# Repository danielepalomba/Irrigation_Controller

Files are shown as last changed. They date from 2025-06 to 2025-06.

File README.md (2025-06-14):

# Irrigation-Controller

## Introduction

This project stems from the need to automate the irrigation of my house's garden so as to make the job easier for my now elderly grandfather. To do this, I decided to build an irrigation control unit that would integrate perfectly with **Home Assistant** already in operation in my house.

## PCB and electrical components

*Caution: 230V mains current can be fatal, in case of doubt or uncertainty, consult a professional!*

First of all, I studied the electrical system, specifically the garden is divided into 3 zones each containing sprinklers controlled by a 24V AC solenoid valve. So as a first step, I installed a transformer that would allow me to obtain the desired voltage from the mains current. Once the power system was complete, I started to study the actual electrical system of the control unit.

The basic idea was to build a control unit consisting mainly of **three modules**:

- *Main board*

- *Relay board*

- *Soil moisture sensor*

There is one problem, however. The ESP32, relay board and sensor are powered by DC, not 24V AC. I therefore installed an AC-DC converter with 12V 5A DC output. 

At this point you may be asking yourself, *Why 12V? It is not possible to power the esp32 with this voltage.* The answer is simple, the relay board needs to be powered at 12V, so to power the esp32 we will need an additional step-down module. Specifically, I chose one based on the LM2596.

So I set to work and using KiCad I created the circuit diagram. 

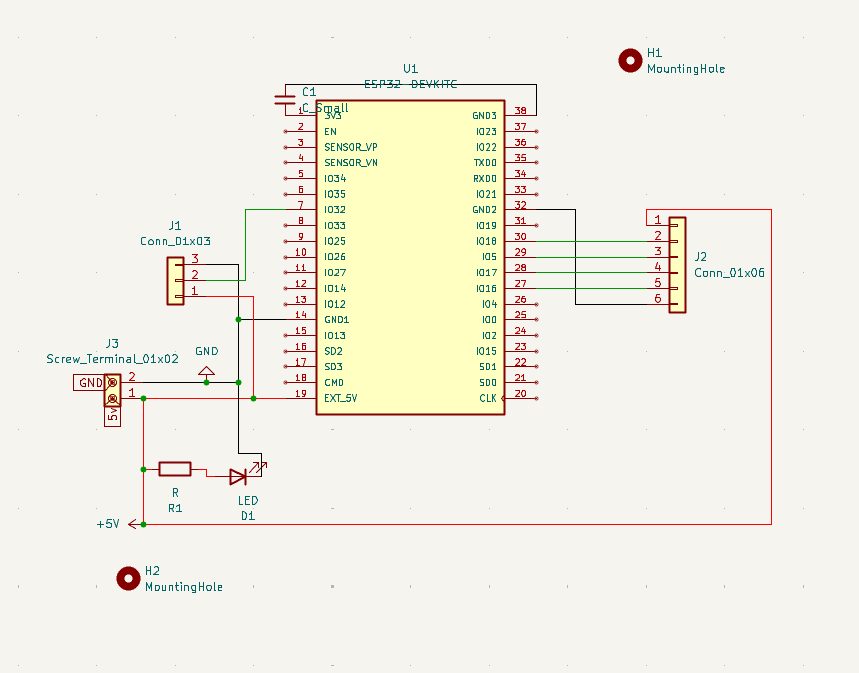
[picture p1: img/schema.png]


- J1, will handle the soil moisture sensor.

- J2 will manage the relay board.

- D1 is simply a status LED.

- C1 is a decoupling capacitor, useful for reducing interference when supplying the board with external 5V.  It should be connected as close as possible to the 3.3V pin.

I then moved on to the modelling of the actual PCB.

 The board will consist of two layers, the upper one for current delivery and the lower one for signal transport. The tracks carrying current to the modules are 0.5mm while those carrying signals are 0.25mm. I then defined the 3mm mounting holes and inserted a ground plane both above and below the board.

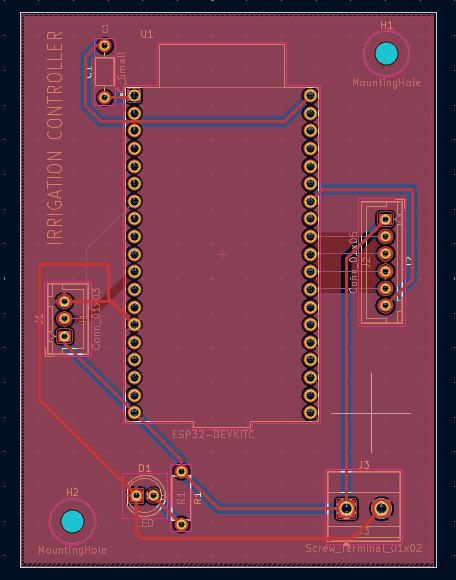
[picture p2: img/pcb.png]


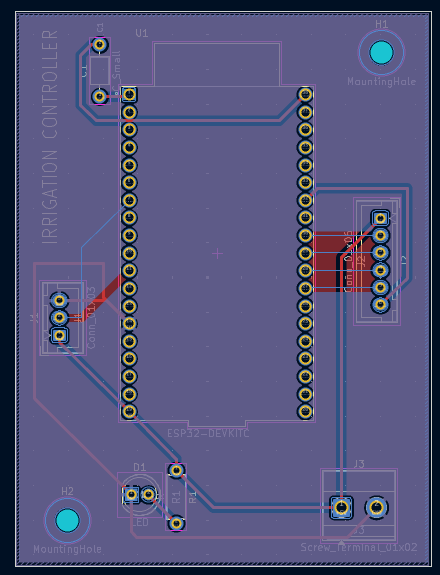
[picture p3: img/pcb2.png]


Once I had completed the card, I sent it to print........and here it is!

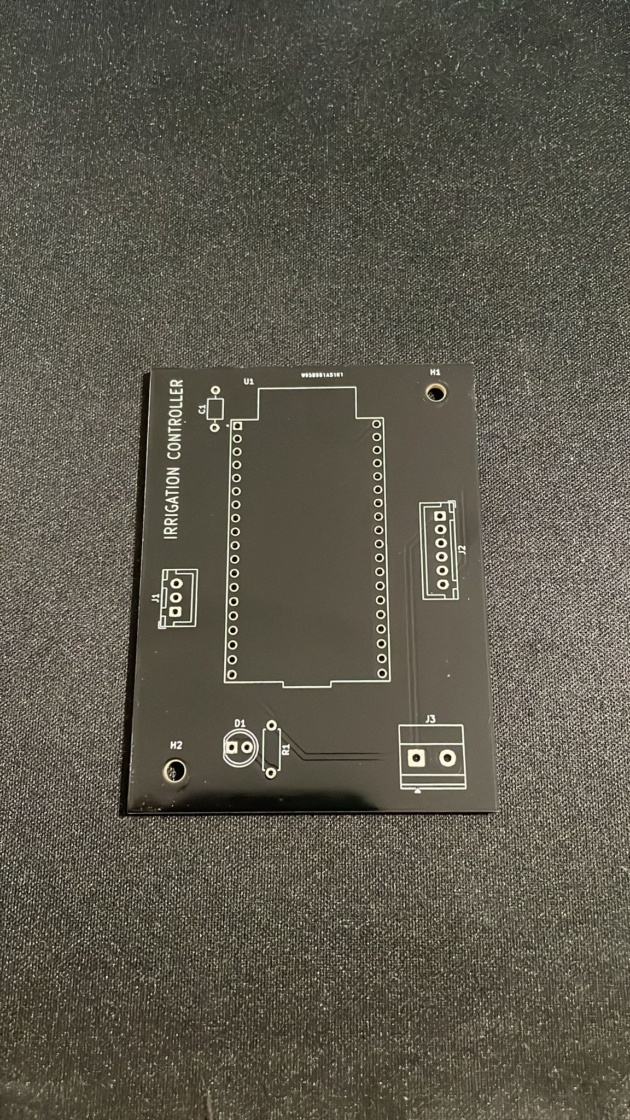
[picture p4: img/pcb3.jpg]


Now that the board was with me, I started soldering all the components. Specifically:

- J3: TerminalBlock_Phoenix:TerminalBlock_Phoenix_MKDS-1,5-2-5.08_1x02_P5.08mm_Horizontal

- R1: 1k Ohm Resistor_THT:R_Axial_DIN0207_L6.3mm_D2.5mm_P7.62mm_Horizontal

- D1 5mm LED

- J1: Connector_JST:JST_XH_B3B-XH-A_1x03_P2.50mm_Vertical

- J2: Connector_JST:JST_XH_B6B-XH-A_1x06_P2.50mm_Vertical

- C1: Capacitor_THT:C_Axial_L3.8mm_D2.6mm_P7.50mm_Horizontal

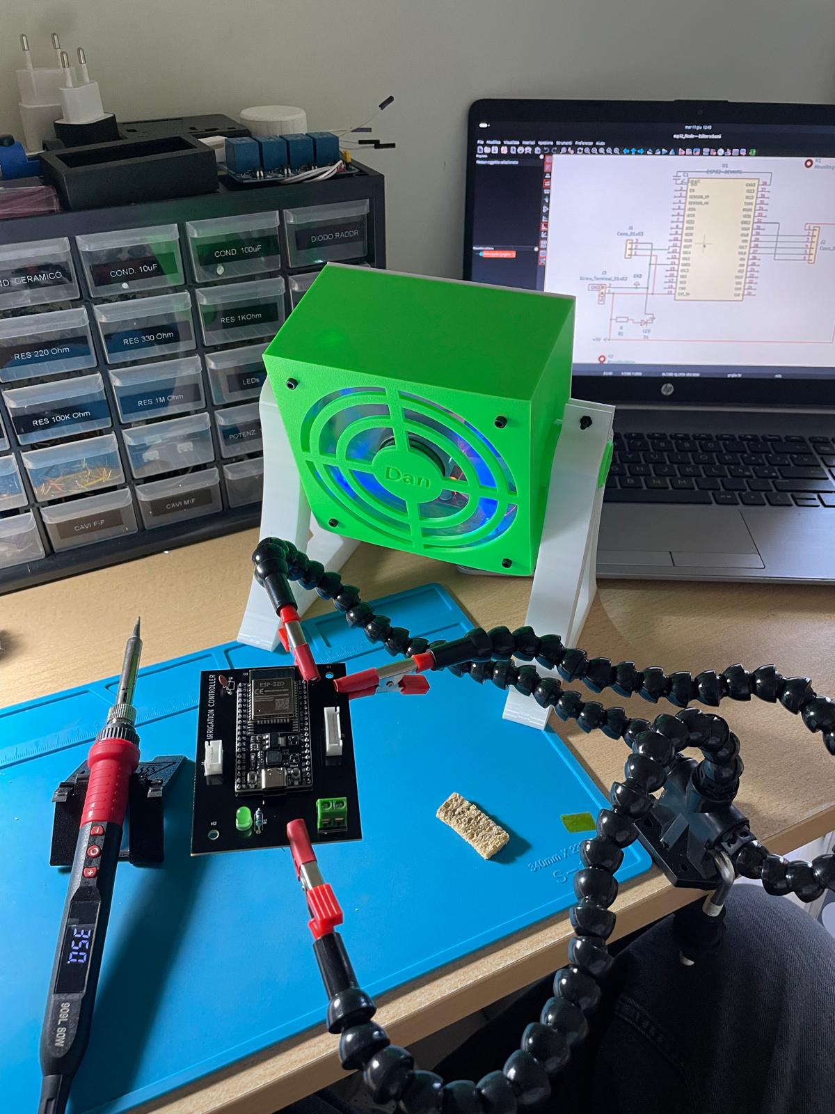
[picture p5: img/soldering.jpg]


The board is finally finished, after which I started thinking of a way to waterproof the soil moisture sensor so that it would withstand the elements.

In the end I modelled a box and printed it with my 3D printer using PETG.  I then inserted the critical part of the board inside and filled the box with epoxy resin.

And this is the end result.

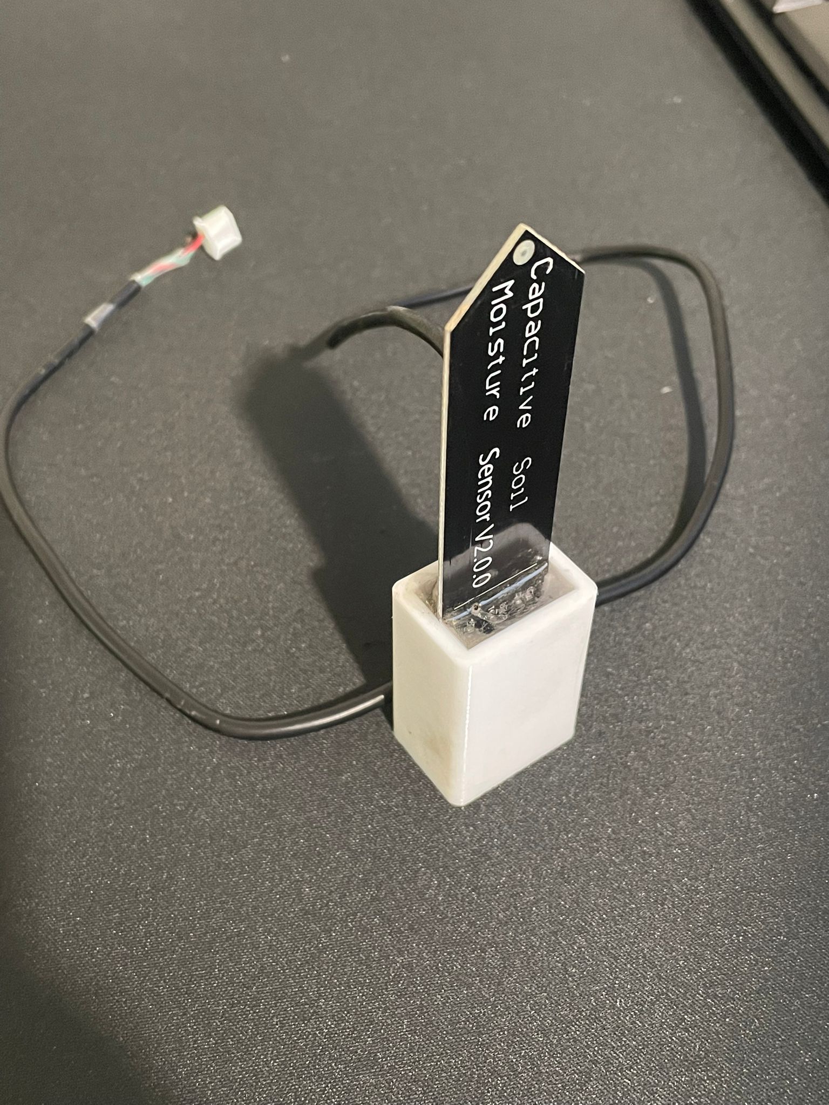
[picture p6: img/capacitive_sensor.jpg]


All components are now ready to be assembled, I will not dwell much on the wiring of the cables as it is only a matter of connecting the solenoid valves to the relays and creating the power supply line to the board, which is very simple and basic.

The end result looks like this:

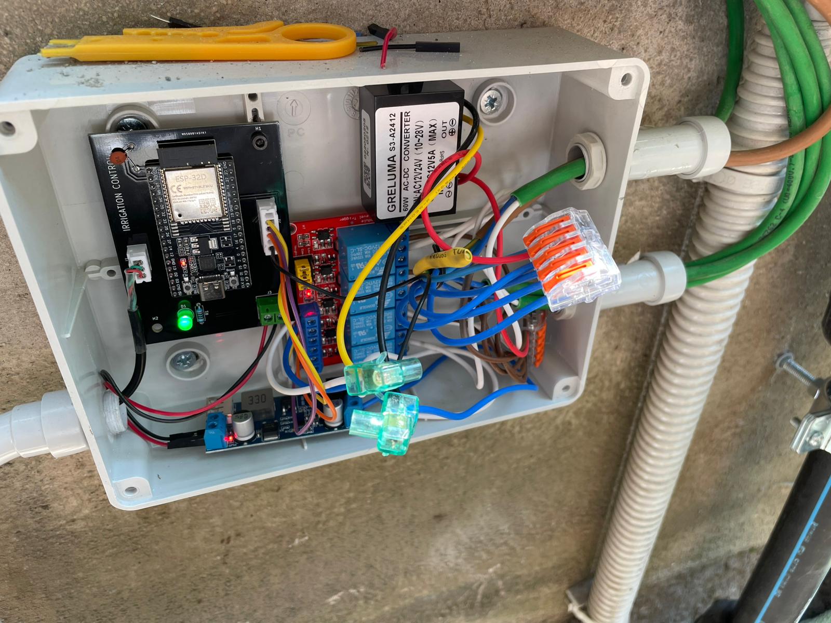
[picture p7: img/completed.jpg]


## ESPHome

Let us now discuss how to make the following board interface with Home Assistant. To do this, I decided to use the very powerful tool, **ESPHome**, thanks to which, via OTA, it is possible to update the board via WiFi without having to use the USB port each time.

So first, let's go to our esphome web interface and add a new device. It will create a new entity for us, open the .yaml file and as a first step, enter the SSID and password of our WiFi. Once this is done, we begin by defining our components.

```yaml
sensor:
  - platform: adc
 pin: GPIO32
 name: "Umidità del terreno (%)"
 update_interval: 30s
 attenuation: 11db
 filters:
      - calibrate_linear:
          - 2.66 -> 0.0
          - 1.080 -> 100.0
      - clamp:
 min_value: 0.0
 max_value: 100.0
 unit_of_measurement: "%"
 accuracy_decimals: 1
```

Values in calibrated linear, must be calculated beforehand. This can be done by immersing the sensor in completely wet soil, the value read out will represent “100%”, while to read the value of “0%” it will be enough to consider the value the sensor transmits without it being immersed in the soil. Each sensor may have different values, so you rely on yours.

```yaml
# Relays (binary switches)
switch:
  - platform: gpio
    name: "Relay 1"
    pin: GPIO18
    id: relay1

  - platform: gpio
    name: "Relay 2"
    pin: GPIO5
    id: relay2

  - platform: gpio
    name: "Relay 3"
    pin: GPIO17
    id: relay3
```

The configuration of relays, on the other hand, is very simple. Each entity will correspond to a button in Home Assistant that will allow each of the 3 solenoid valves to be powered or not.

Everything is ready, let's upload and check that the board is online, you can see any errors through the logs that esphome provides.

## Home assistant

Now open *Home Assistant -> Settings -> Devices and Services*. We should see our entity automatically recognised on the network by HA. In case it is not there, you can add it directly using its IP address.

Once our device has been added, the buttons to control the relays and the soil moisture percentage will be shown on the main dashboard. At this point we need to create the logic of an actual irrigation controller, to do this we will use the automations and partially modify the HA *configuration.yaml*.

First, we look for the HA configuration file and add the following entities to it.

```yaml
input_number:
  durata_irrigazione_zona_1:
    name: Durata irrigazione zona 1
    initial: 10
    min: 1
    max: 30
    step: 1
    unit_of_measurement: 'min'

  durata_irrigazione_zona_2:
    name: Durata irrigazione zona 2
    initial: 10
    min: 1
    max: 30
    step: 1
    unit_of_measurement: 'min'

  durata_irrigazione_zona_3:
    name: Durata irrigazione zona 3
    initial: 10
    min: 1
    max: 30
    step: 1
    unit_of_measurement: 'min'

timer:
  irrigazione_zona_1:
    duration: '00:05:00'
    name: Timer irrigazione zona 1

  irrigazione_zona_2:
    duration: '00:05:00'
    name: Timer irrigazione zona 2

  irrigazione_zona_3:
    duration: '00:05:00'
    name: Timer irrigazione zona 3

input_boolean:

  zona1_lunedi:
    name: Zona 1 - Lunedì
  zona1_martedi:
    name: Zona 1 - Martedì
  zona1_mercoledi:
    name: Zona 1 - Mercoledì
  zona1_giovedi:
    name: Zona 1 - Giovedì
  zona1_venerdi:
    name: Zona 1 - Venerdì
  zona1_sabato:
    name: Zona 1 - Sabato
  zona1_domenica:
    name: Zona 1 - Domenica

  zona2_lunedi:
    name: Zona 2 - Lunedì
  zona2_martedi:
    name: Zona 2 - Martedì
  zona2_mercoledi:
    name: Zona 2 - Mercoledì
  zona2_giovedi:
    name: Zona 2 - Giovedì
  zona2_venerdi:
    name: Zona 2 - Venerdì
  zona2_sabato:
    name: Zona 2 - Sabato
  zona2_domenica:
    name: Zona 2 - Domenica

  zona3_lunedi:
    name: Zona 3 - Lunedì
  zona3_martedi:
    name: Zona 3 - Martedì
  zona3_mercoledi:
    name: Zona 3 - Mercoledì
  zona3_giovedi:
    name: Zona 3 - Giovedì
  zona3_venerdi:
    name: Zona 3 - Venerdì
  zona3_sabato:
    name: Zona 3 - Sabato
  zona3_domenica:
    name: Zona 3 - Domenica

input_datetime:
  zona1_orario_avvio:
    name: Orario irrigazione Zona 1
    has_time: true
    has_date: false

  zona2_orario_avvio:
    name: Orario irrigazione Zona 2
    has_time: true
    has_date: false

  zona3_orario_avvio:
    name: Orario irrigazione Zona 3
    has_time: true
    has_date: false
```

These are all entities that will come in handy later to control our devices. **Restart home assistant.**

Four basic automations are provided for each zone:

- Turning on sprinklers

- Switching off sprinklers when timer expires

- Forced sprinkler shutdown

- Programmed start-up of sprinklers

Since the code of the automations of the 3 zones is the same, we will only study zone 1, as the others are easily replicable.

---

> In case you want to replicate the project, remember to use the exact name of your entities.

### Turning on sprinklers

```yaml
alias: "Accensione irrigatore zona 1 "
description: ""
triggers:
  - trigger: state
    entity_id:
      - switch.test_relay_3
    from: "off"
    to: "on"
conditions: []
actions:
  - target:
      entity_id: timer.irrigazione_zona_1
    data:
      duration: |
        {{ states('input_number.durata_irrigazione_zona_1') | int * 60 }}
    action: timer.start
mode: single
```

### Switching off sprinklers when timer expires

```yaml
alias: Spegnimento interruttore zona 1
description: ""
triggers:
  - trigger: event
    event_type: timer.finished
    event_data:
      entity_id: timer.irrigazione_zona_1
conditions: []
actions:
  - action: switch.turn_off
    metadata: {}
    data: {}
    target:
      entity_id: switch.test_relay_3
mode: single
```

### Forced sprinkler shutdown

```yaml
alias: Spegnimento forzato
description: ""
triggers:
  - trigger: state
    entity_id:
      - switch.test_relay_3
    from: "on"
    to: "off"
conditions: []
actions:
  - data:
      entity_id: timer.irrigazione_zona_1
    action: timer.cancel
mode: single
```

### Programmed start-up of sprink

```yaml
alias: Irrigazione automatica Zona 1
description: ""
triggers:
  - at: input_datetime.zona1_orario_avvio
    trigger: time
conditions:
  - condition: template
    value_template: |
      {% set oggi = now().weekday() %} {% set giorni = {
        0: states('input_boolean.zona1_lunedi'),
        1: states('input_boolean.zona1_martedi'),
        2: states('input_boolean.zona1_mercoledi'),
        3: states('input_boolean.zona1_giovedi'),
        4: states('input_boolean.zona1_venerdi'),
        5: states('input_boolean.zona1_sabato'),
        6: states('input_boolean.zona1_domenica')
      } %} {{ giorni[oggi] == 'on' }}
actions:
  - target:
      entity_id: switch.test_relay_1
    action: switch.turn_on
    data: {}
  - delay:
      seconds: >-
        {{ (states('input_number.durata_irrigazione_zona_1') | float * 60) | int
        }}
  - target:
      entity_id: switch.test_relay_1
    action: switch.turn_off
    data: {}
mode: single
```

It is then possible to create a customised plate to facilitate sensor management, I specifically set it up like this.

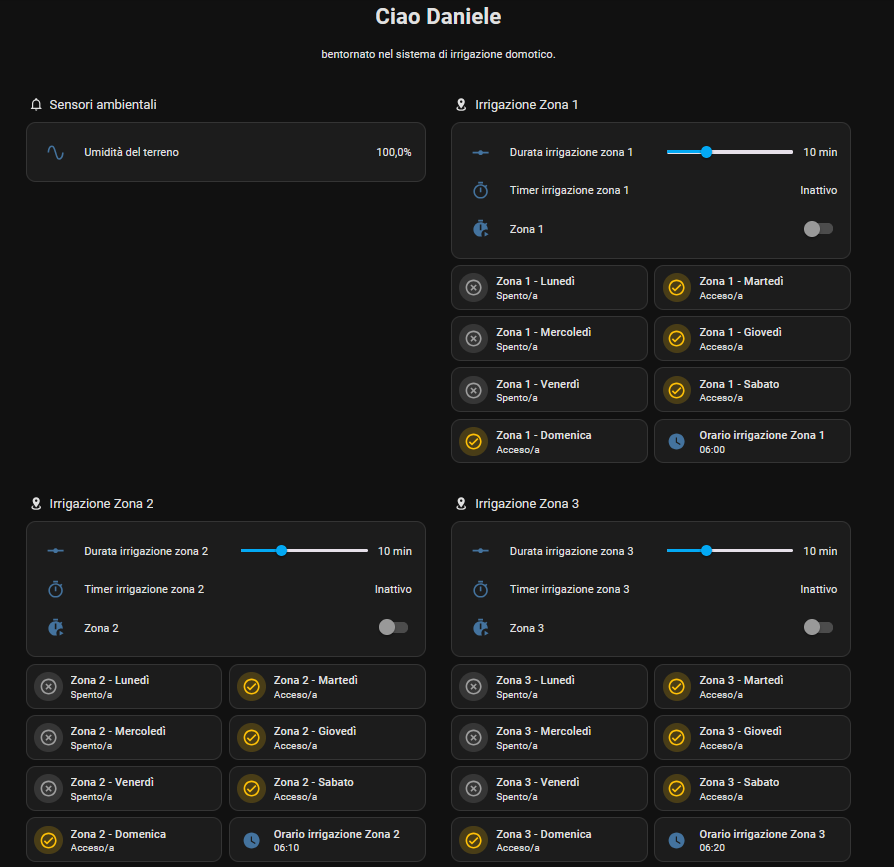
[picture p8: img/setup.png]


Let's try it!

gif

Home Assistant offers a way of customisation possibilities, and it is possible to add many other features to this system, such as notifications, automatic switch-on based on the humidity sensor and much more.

---

*Thank you all, see you at the next project.*

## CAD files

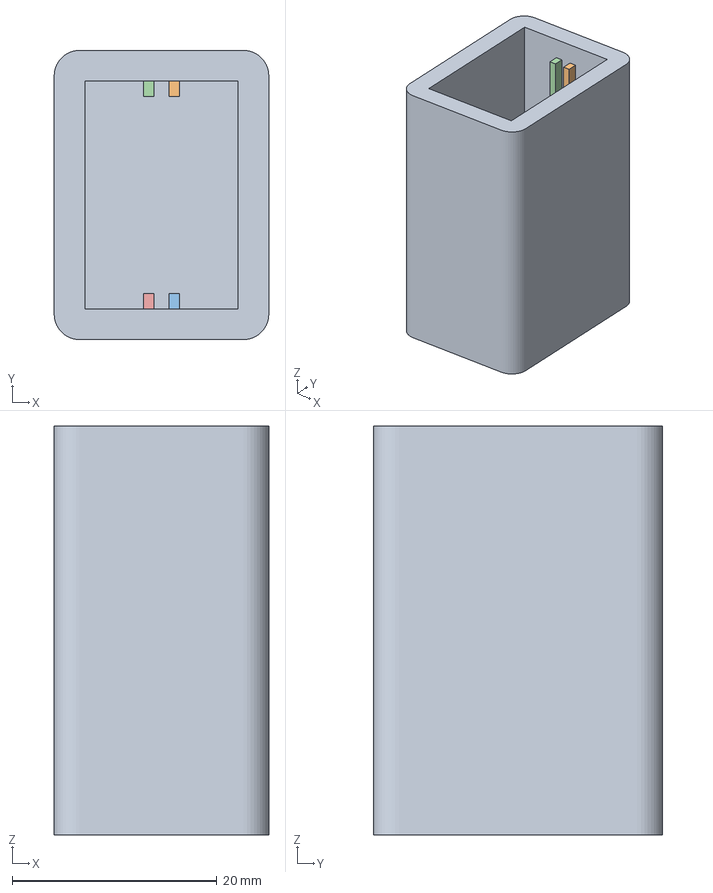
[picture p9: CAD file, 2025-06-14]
3D model/box.3mf
21.0 x 28.3 x 40.0 mm
Corpo1
Corpo6
Corpo7
Corpo8
Corpo9
